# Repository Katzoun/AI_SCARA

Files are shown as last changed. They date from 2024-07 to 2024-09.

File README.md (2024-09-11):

# **AI.SCARA** – The low-cost SCARA robot 
## Abstract
The aim of this project was to design and build a low-cost robot based on the industrial concept SCARA, which meets the requirements in terms of rigidity and repeatability for application in a wide range of manipulation tasks primarily implemented in a university environment. The project includes not only the mechanical design, but also design and implementation of the electrical circuitry, control system, and design of a human-machine graphical interface for basic controland diagnosis of the robotic structure.
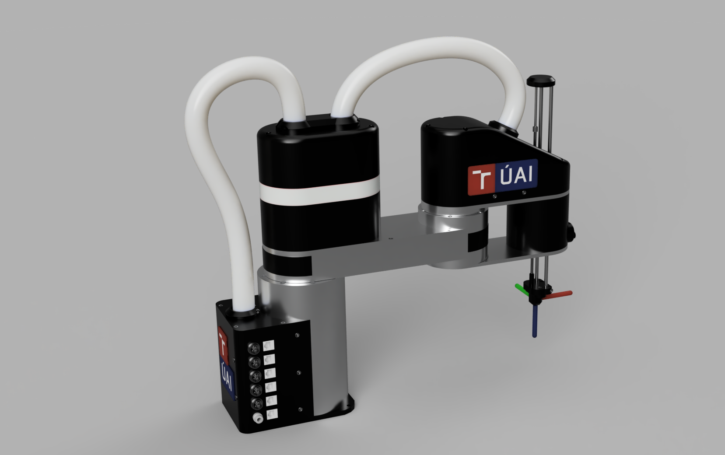
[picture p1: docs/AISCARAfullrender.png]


## Video demontration
Watch the video (https://youtube.com/watch?v=5lQ4tVK84JA)
## Repository Index
* [AISCARA_ControlSystem](https://github.com/Katzoun/AI_SCARA/tree/main/AISCARA_ControlSystem) - Source codes for AISCARA control system
* [AISCARA_GUI](https://github.com/Katzoun/AI_SCARA/tree/main/AISCARA_GUI) - Source codes for AISCARA user interface
* [docs](https://github.com/Katzoun/AI_SCARA/tree/main/docs) - Misc documentation files 
* [parts](https://github.com/Katzoun/AI_SCARA/tree/main/parts) - stl files of all components (with list of all parts)

## Mechanical design
The mechanical structure of the robot consists of aluminium parts combined with 3D printed parts. The combination of 3D printing and metal machining provides good rigidity and a reasonable price. In addition, all metal components are designed to be manufactured on conventional machines (mill and lathe) without numerical control. The mechanical design also includes the design of the electrical control cabinet. All parts of the robot were designed in Fusion 360.

The robot design consists of three key units - **the stationary base, the first arm and the second arm.** 
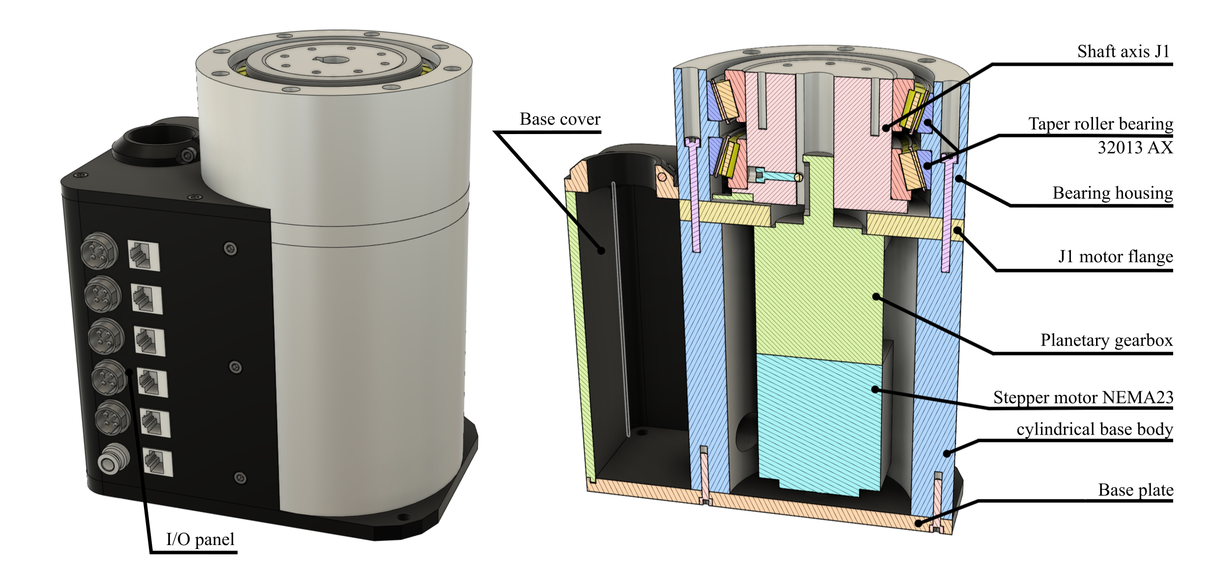
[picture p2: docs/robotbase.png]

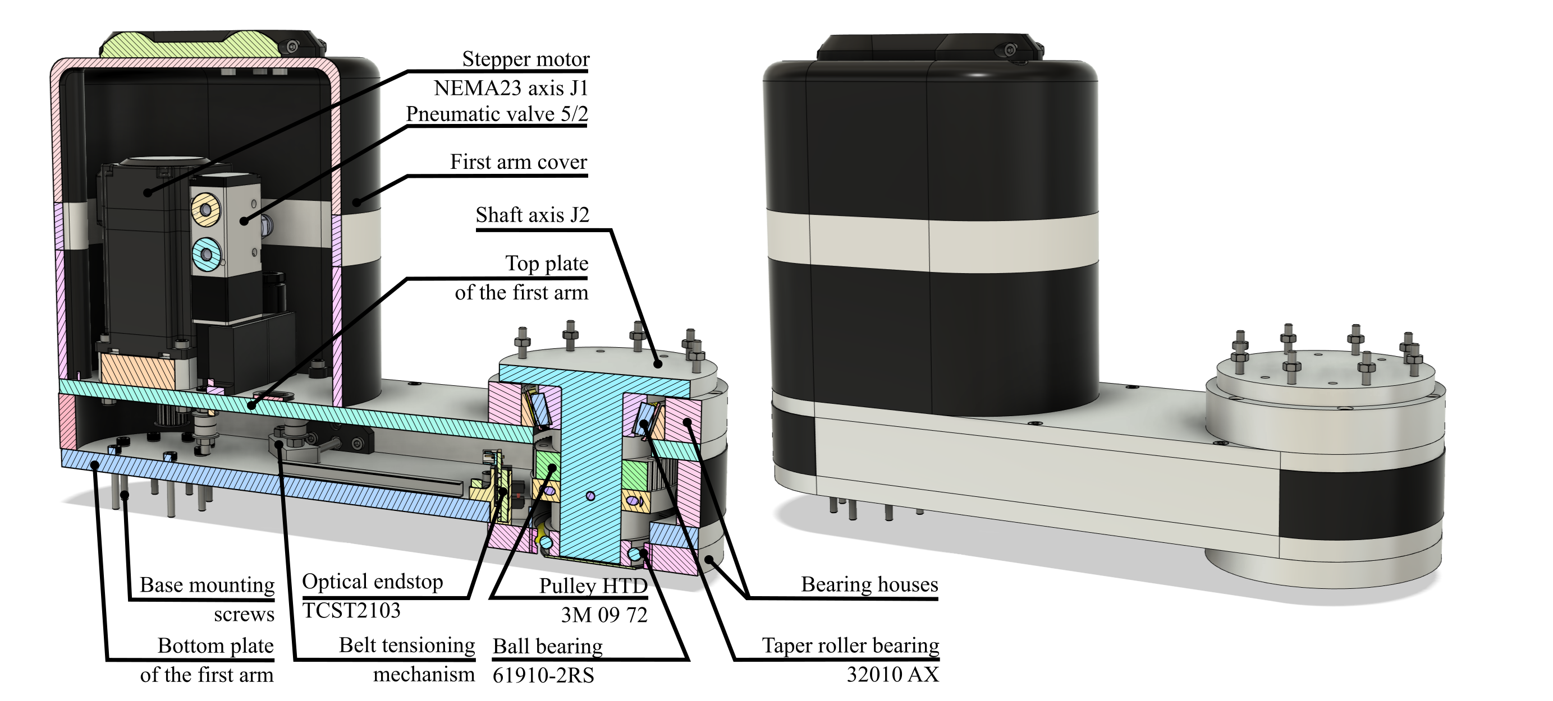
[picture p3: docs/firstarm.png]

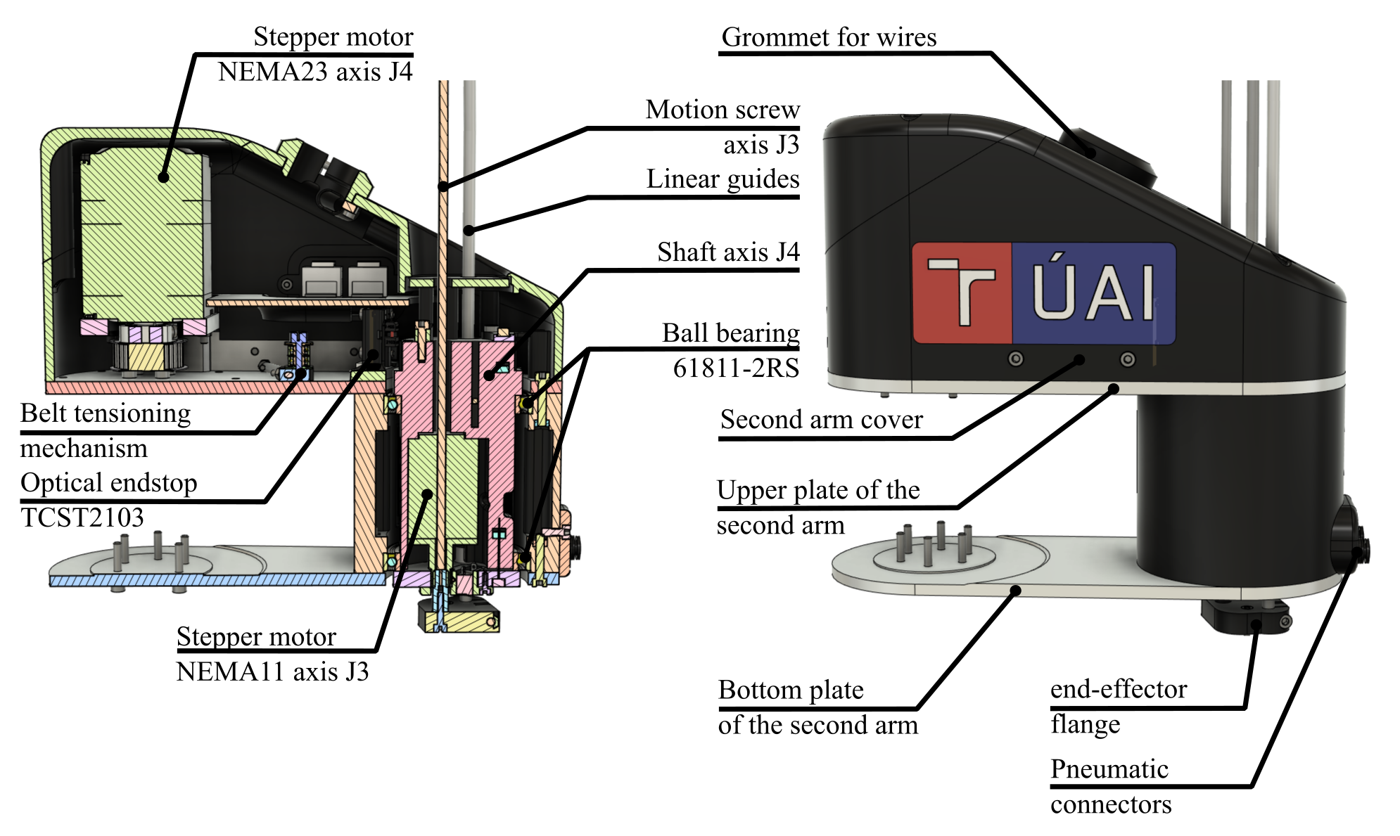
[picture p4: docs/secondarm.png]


## Electrical design
Stepper motors with encoders were chosen to drive the robot. The main advantage of these motors is their very low purchase price compared to equally powerful servo drives. By controlling stepper motors in a closed loop, better dynamic characteristics can be achieved compared to open-loop stepper motors. Another indisputable advantage of closed-loop control is the possibility of position correction in case of overload. Reference position detection is provided by optical limit switches (TCST2103).

**List of used stepper motors** 
* J1 - NEMA23 [23HS22-2804-ME1K ](https://www.omc-stepperonline.com/nema-23-closed-loop-stepper-motor-1-2nm-166-7oz-in-with-magnetic-encoder-1000ppr-4000cpr-23hs22-2804-me1k) with precision planetary gearbox VRL-070C
* J2 - NEMA23 [1-CL57T-S20-V41 ](https://www.omc-stepperonline.com/ts-series-2-0-nm-283-28oz-in-1-axis-closed-loop-stepper-cnc-kit-nema-23-motor-driver-1-cl57t-s20-v41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)
* J3 - NEMA11 [11N18S0754GD-250RS ](https://www.omc-stepperonline.com/nema-11-non-captive-46mm-stack-0-75a-lead-2-54mm-0-1-length-250mm-11n18s0754gd-250rs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)
* J4 - NEMA23 [1-CL57T-S12-V41 ](https://www.omc-stepperonline.com/ts-series-1-2-nm-170oz-in-1-axis-closed-loop-stepper-cnc-kit-nema-23-motor-driver-1-cl57t-s12-v41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)

The robot controller (shown below) brings together all the electronic components necessary for the proper functioning of the AI.SCARA robot - i.e. stepper motor controllers, microcontrollers that run the control system, power supplies and many others. Power is provided by three DC power supplies - LRS-350-36 (CL57 stepper drivers), LRS-100-12 (pneumatic equipment, DM320T driver, internal air compressors etc.) and RS-25-5 (MCUs).

There are two microcontrollers in the SCARA robot controller. The main MCU is the Teensy 4.1, which performs all the kinematic calculations for the robot's movements.
The reason for choosing the Teensy 4.1 microcontroller for robot motion control was mainly due to its architecture, which is compatible with user-friendly Arduino microcontrollers. The control of the robot peripherals is provided by Arduino Nano. 

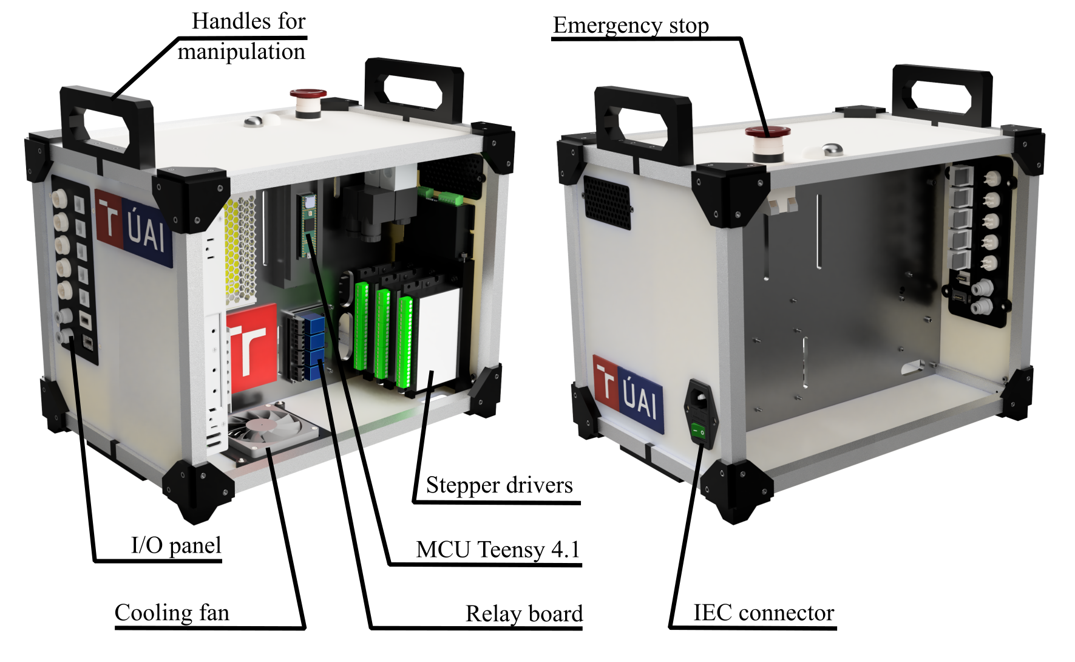
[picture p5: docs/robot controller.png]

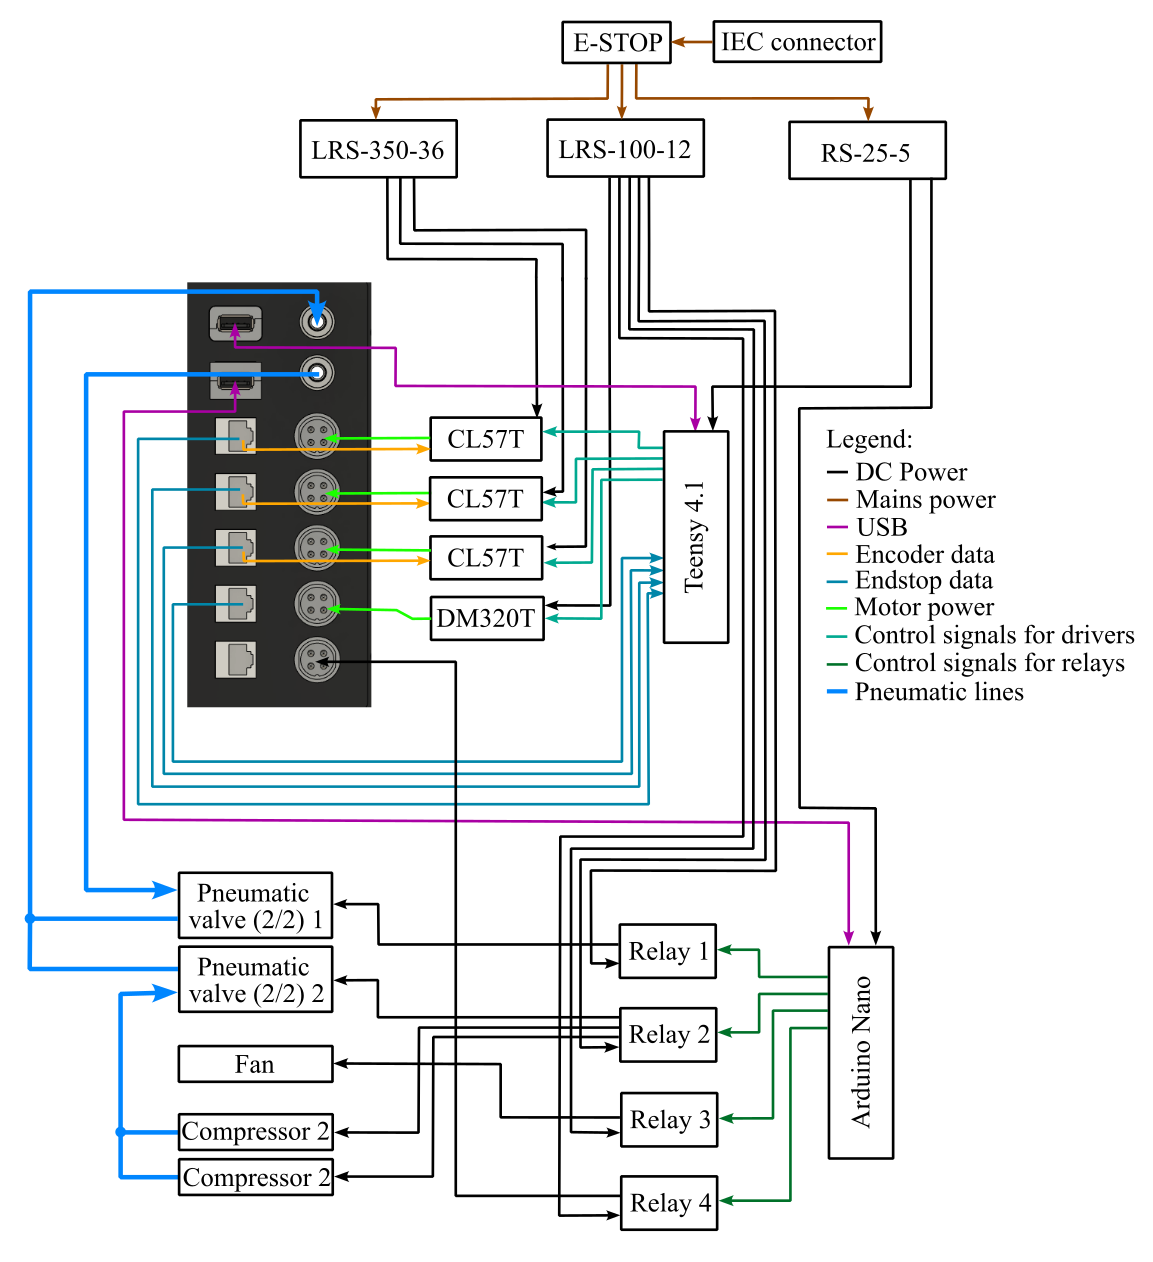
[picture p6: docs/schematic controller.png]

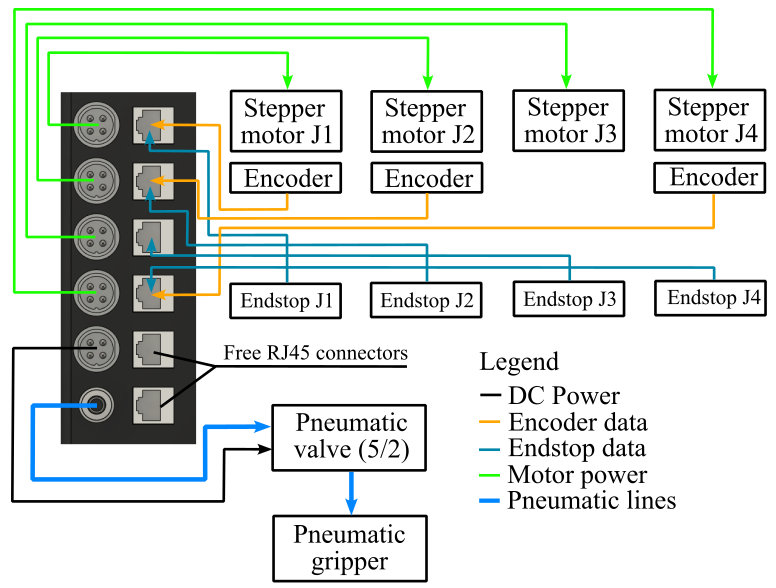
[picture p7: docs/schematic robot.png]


## Software

The control software is a key component of the robotic arm. The proposed system simultaneously performs the control and precise synchronization of all four axes of the robot, analytically solves kinematic calculations for maximum computational efficiency, controls the current position of the axes and, last but not least, controls the robot peripherals. 
**The control software running in the robot controller consists of two parts:**

* [AISCARA teensy board](https://github.com/Katzoun/AI_SCARA/tree/main/AISCARA_ControlSystem/AISCARA%20teensy%20board)
* [AISCARA nano board](https://github.com/Katzoun/AI_SCARA/tree/main/AISCARA_ControlSystem/AISCARA%20nano%20board)

For easy interaction with the robot, a user-friendly graphical interface has been created that allows, among other things, simple diagnostics and programming of the robot's movements.

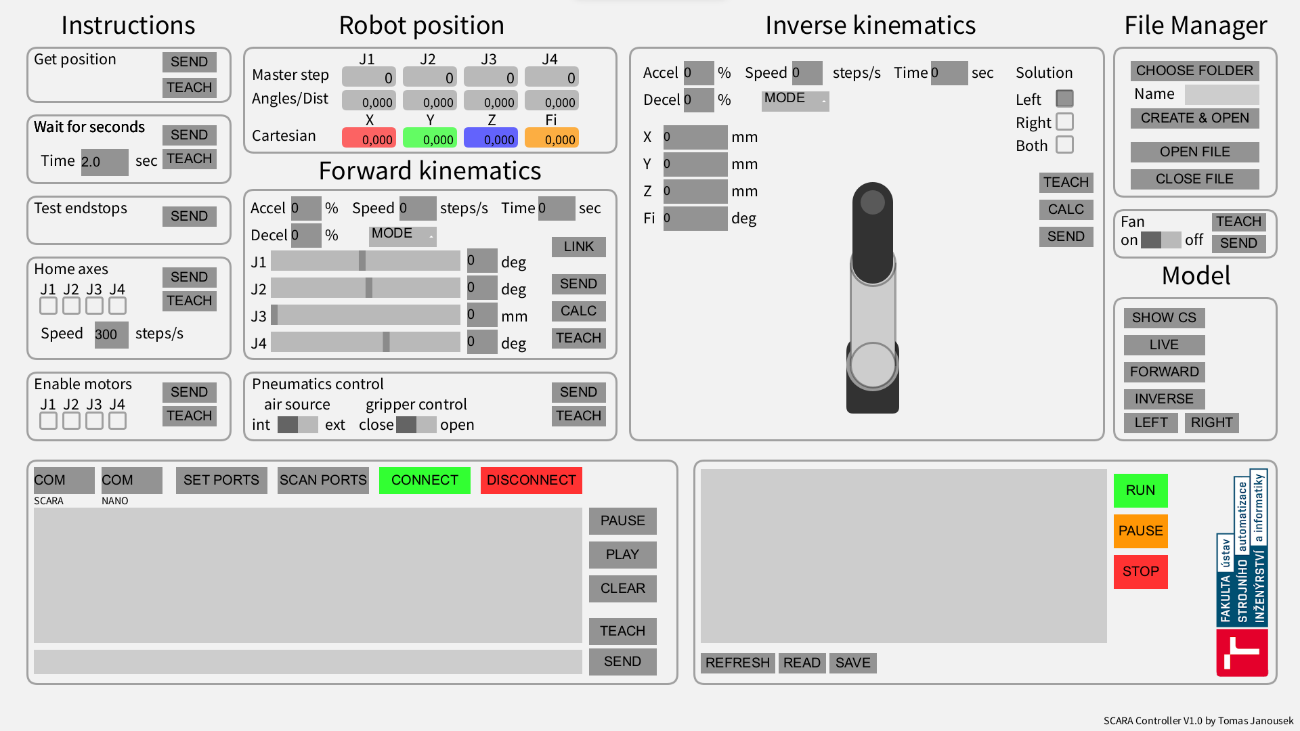
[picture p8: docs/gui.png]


In the lower left corner there is a console where error messages and other information concerning the controller operation are displayed. Below the console there is a command line for manual instruction input. Manual input is particularly useful when testing additional programmed functionalities that are not represented graphically in the interface. To visually check the robot's position, the interface also includes a dynamic 2D model that can operate in three modes. In Live mode, the model displays the position in which the robot is currently physically located. The remaining modes (Forward and Inverse) are simulation modes and are used to visually represent the forward and inverse kinematics solutions. 

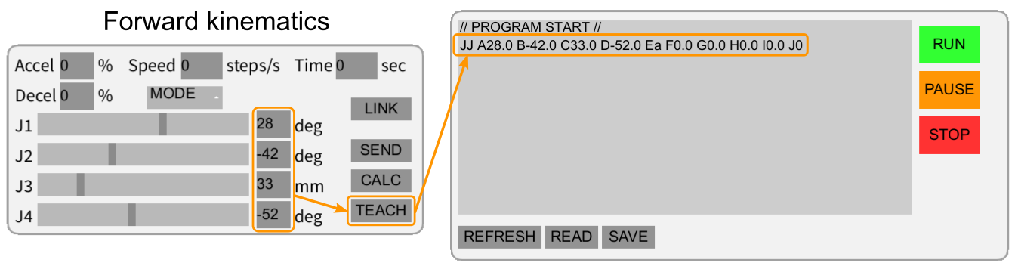
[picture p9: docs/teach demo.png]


Within the proposed interface, the SCARA robot can also be easily programmed in addition to those already mentioned. For most of the instructions, there is a "Teach" button which saves the instruction into the program memory. The entire program is then displayed in a text box to the right of the console. For working with program files, there is a simple file manager in the GUI. Through it you can open already created programs or create completely new ones.

### Establishing communication with the AI.SCARA robot controller
For successful communication between the personal computer and the controller it is first necessary to connect these units via the USB interface. The "scan ports" button is intended to make it easier to find the ports to which the controller is connected. After pressing the "scan ports" button, the console lists the currently used ports of the personal computer. The user interface cannot yet automatically detect which of these ports the controller is on, so the user must manually enter the port names in the appropriate fields. The process of establishing a connection can be initiated with the "connect" button. The connection process is shown in the figure below.
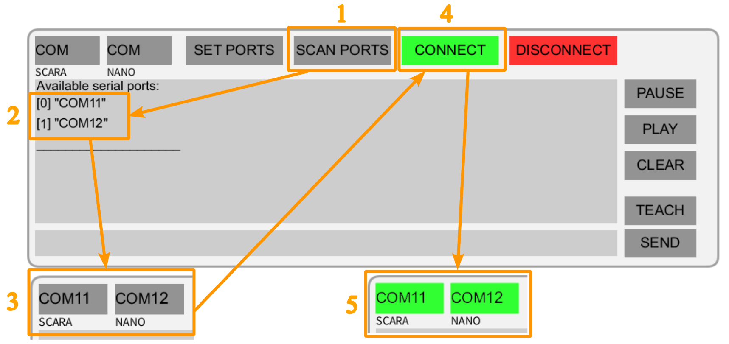
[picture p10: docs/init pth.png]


## Result
After successful assembly and debugging, the designed robotic structure was subjected to a series of tests aimed at verifying the basic "metrological" characteristics of the robot. The measurements performed were divided into three main categories - repeatability tests, stiffness tests and complex tests, which are a combination of the previous two. The repeatability of the robot was estimated to be within a few tenths of a millimetre based on the tests performed. 
Again, it should be noted that the measurements made provide only a very basic idea of the metrological characteristics of the proposed solution. The measurement results are influenced not only by the mechanical design but also by the motion control of the robot. A more precise set of validation tests, including a more advanced statistic evaluation, could be addressed in future work. The table below shows the basic technical parameters of the proposed robot.

| Parameter | Value |
| --- | --- |
| Horizontal reach (X-Y)  | 400 mm  |
| Vertical reach (Z) | 170 mm  |
| Payload | 1 kg |
| Repeatability | tenths of millimetre |
| Max. speed J1 | 120 °/s |
| Max. speed J2 | 120 °/s |
| Max. speed J3 | 80 mm/s |
| Max. speed J4 | 160 °/s |
| Axis range J1 | -116° to +125° |
| Axis range J2 | -129° to +120° |
| Axis range J3 | 170 mm |
| Axis range J4 | -190° to +120° |
| Robot weight | 17 kg |
| Controller weight | 8 kg |
| Build price | approx. 1500 €| 

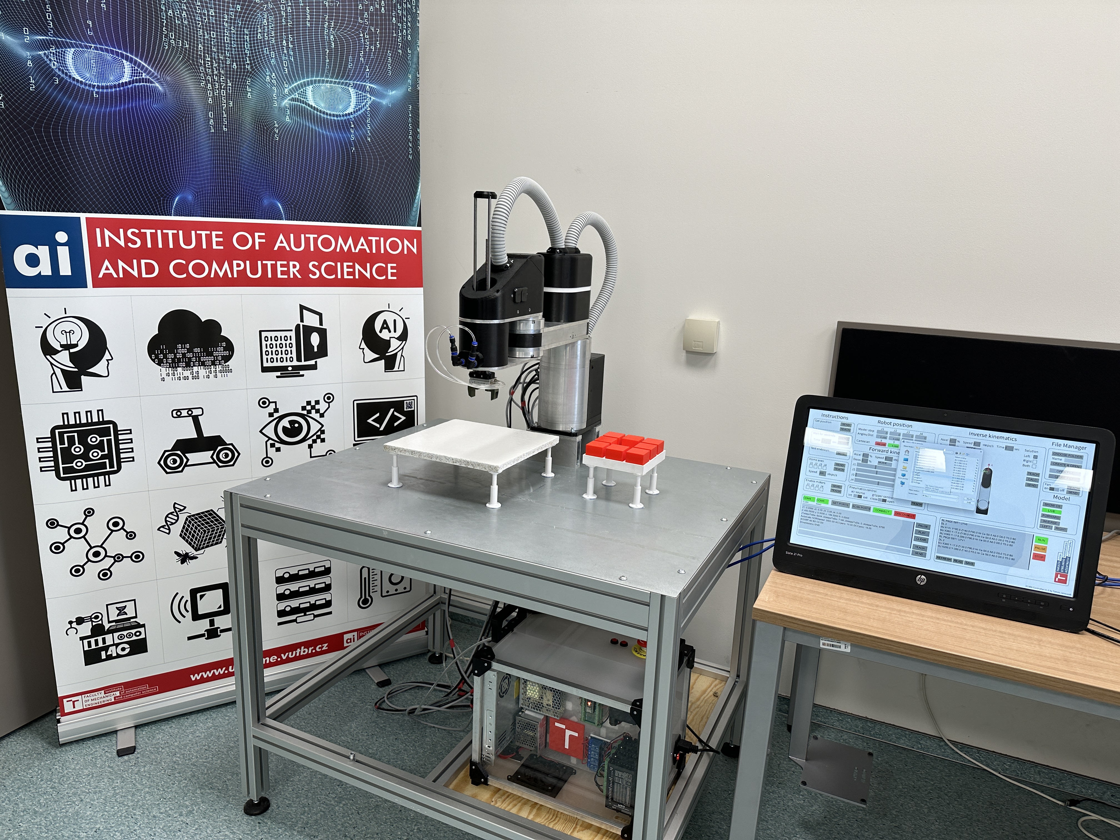
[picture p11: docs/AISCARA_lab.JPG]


## Contact info
For more information and details about this project please contact me on
tomas.janousek02@gmail.com

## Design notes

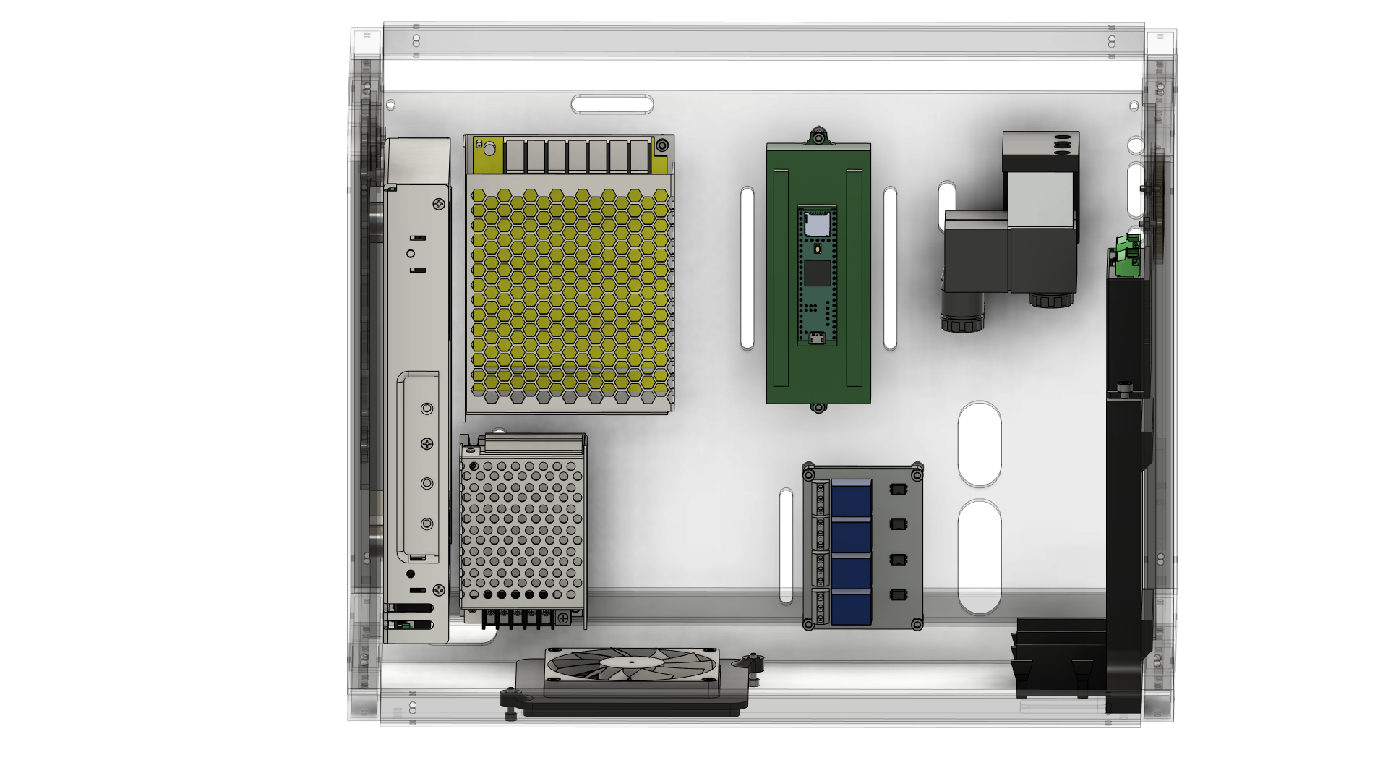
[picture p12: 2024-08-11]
docs/img controller/controlbox op20 v1.png

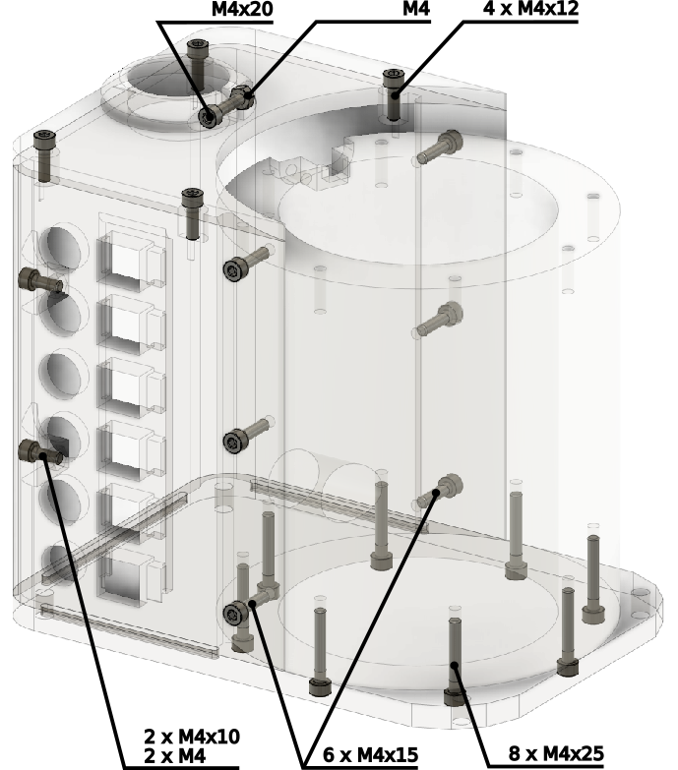
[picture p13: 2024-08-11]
docs/img base/base1 pth.png

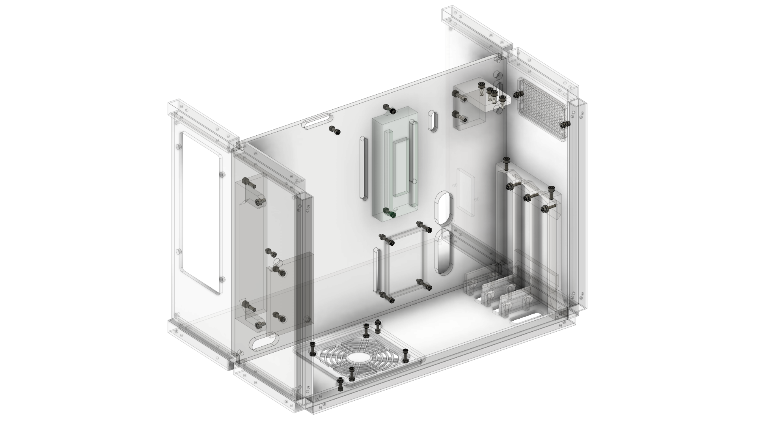
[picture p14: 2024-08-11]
docs/img controller/controlbox op20 v6.png

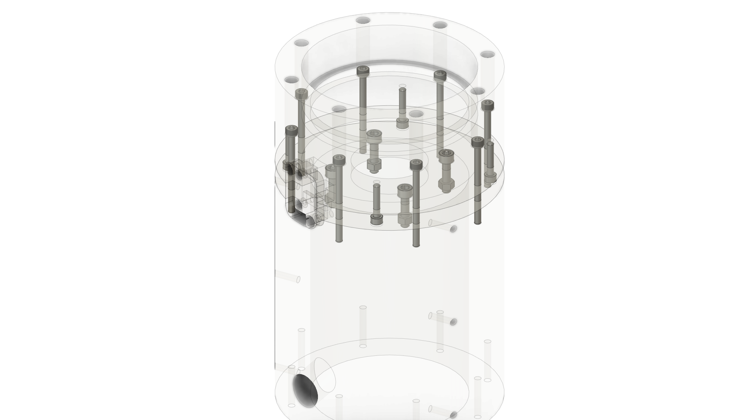
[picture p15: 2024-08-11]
docs/img base/base2.png

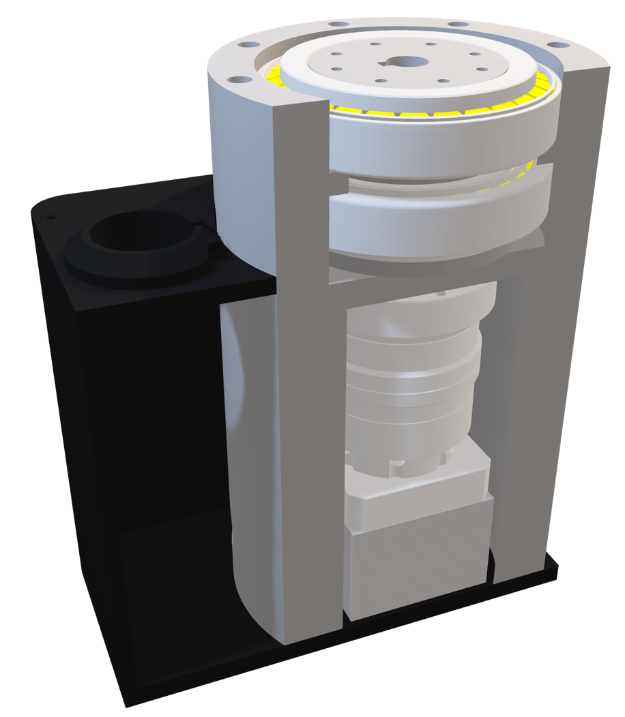
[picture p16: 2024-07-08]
docs/base.png

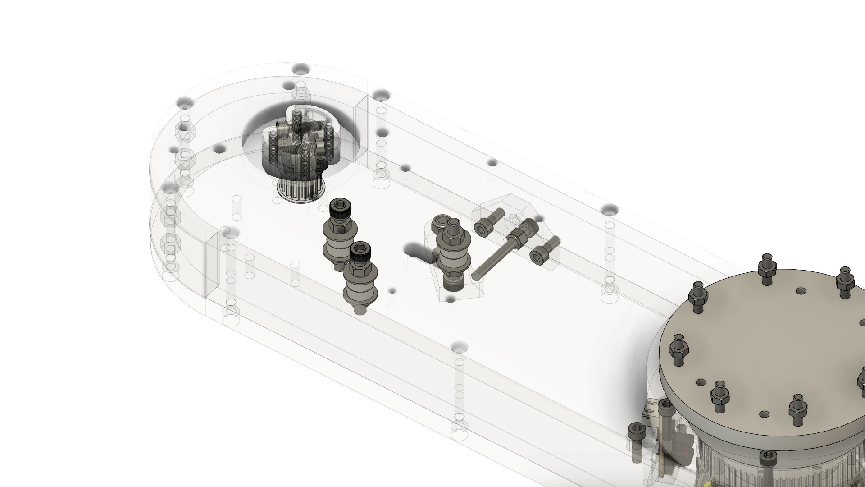
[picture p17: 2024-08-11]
docs/img first arm/arm 3 prev v63 3.png

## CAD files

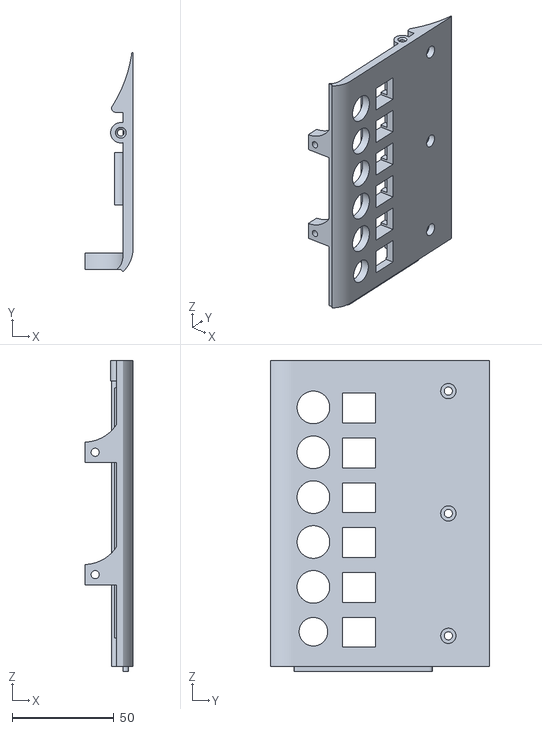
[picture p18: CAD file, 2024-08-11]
parts/base/Base cover (front).stl
23.5 x 107.6 x 152.5

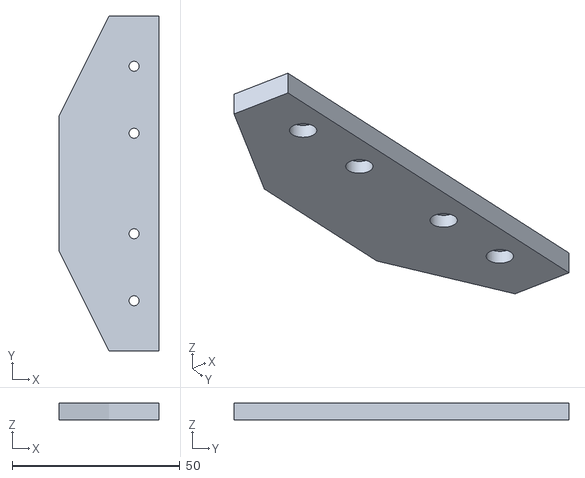
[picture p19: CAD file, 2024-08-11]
parts/controller/Longitudinal control box cover.stl
30.0 x 100.0 x 5.00

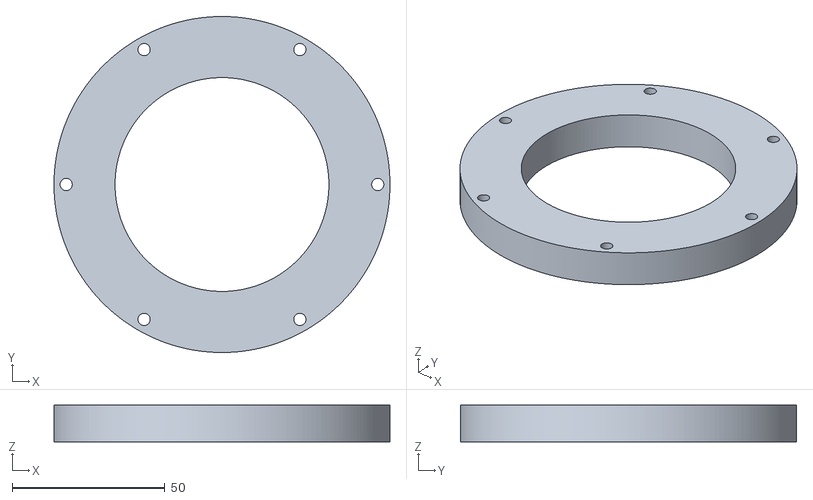
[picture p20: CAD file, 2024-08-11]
parts/first arm/First arm bearing housing (bottom).stl
110.0 x 110.0 x 12.0

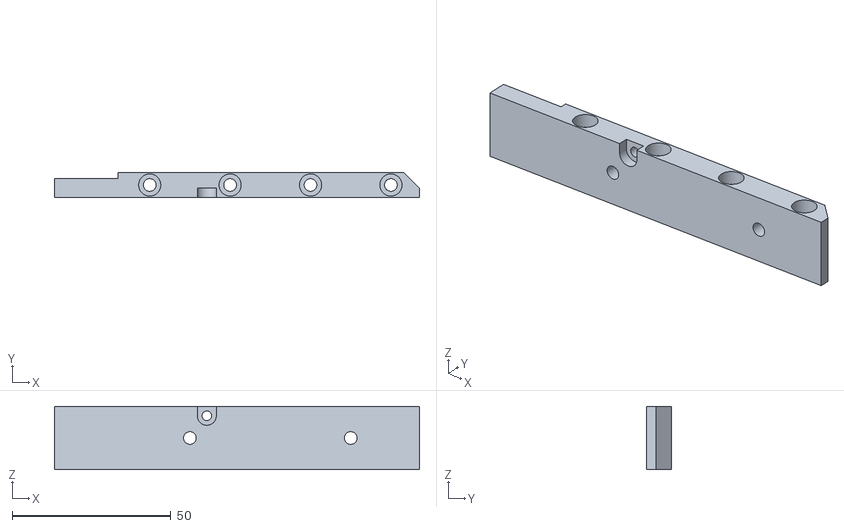
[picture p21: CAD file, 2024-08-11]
parts/second arm/Second arm reinforcement.stl
115.0 x 8.00 x 20.0

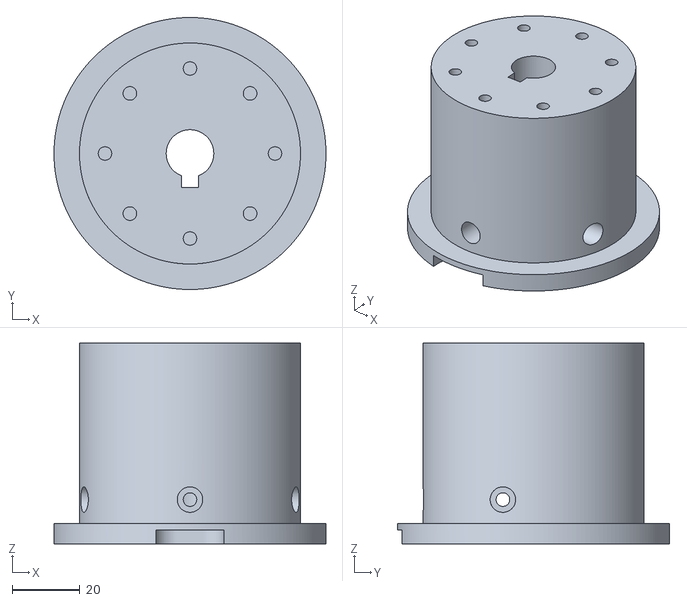
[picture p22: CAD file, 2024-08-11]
parts/base/Shaft axis J1.stl
80.0 x 80.0 x 59.0

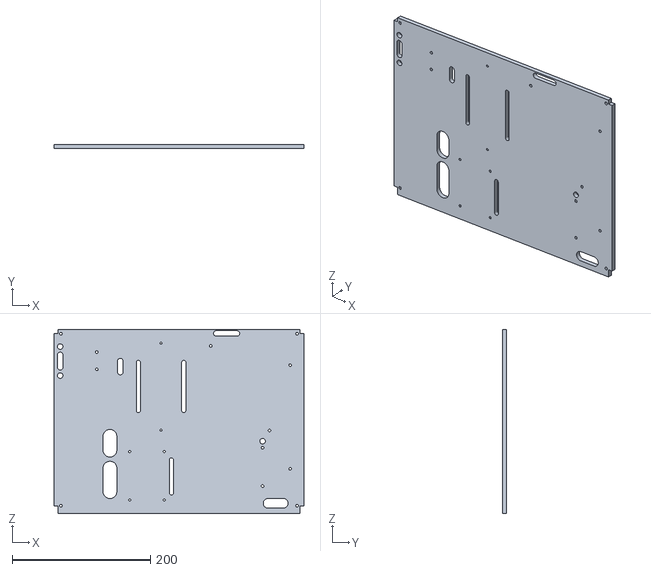
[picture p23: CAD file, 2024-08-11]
parts/controller/White plexiglass 362x267x6 mm - middle panel.stl
362.0 x 6.00 x 267.0

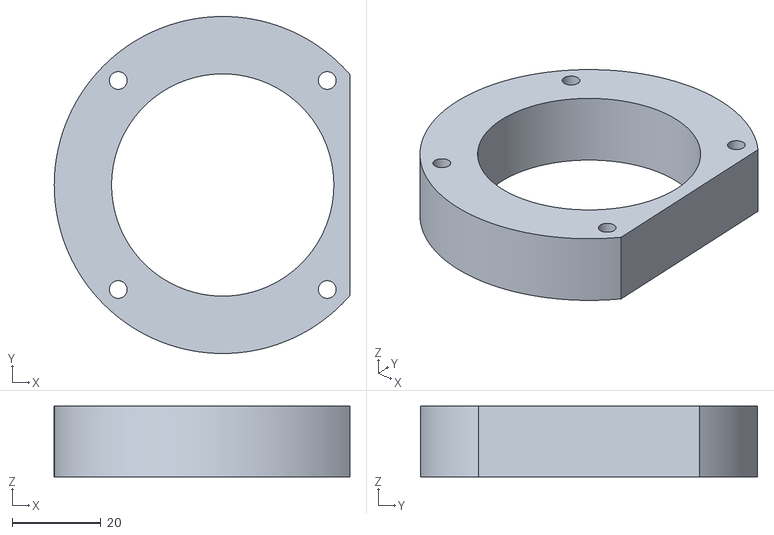
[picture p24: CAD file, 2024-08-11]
parts/first arm/J2 motor mount.stl
66.6 x 76.0 x 16.0

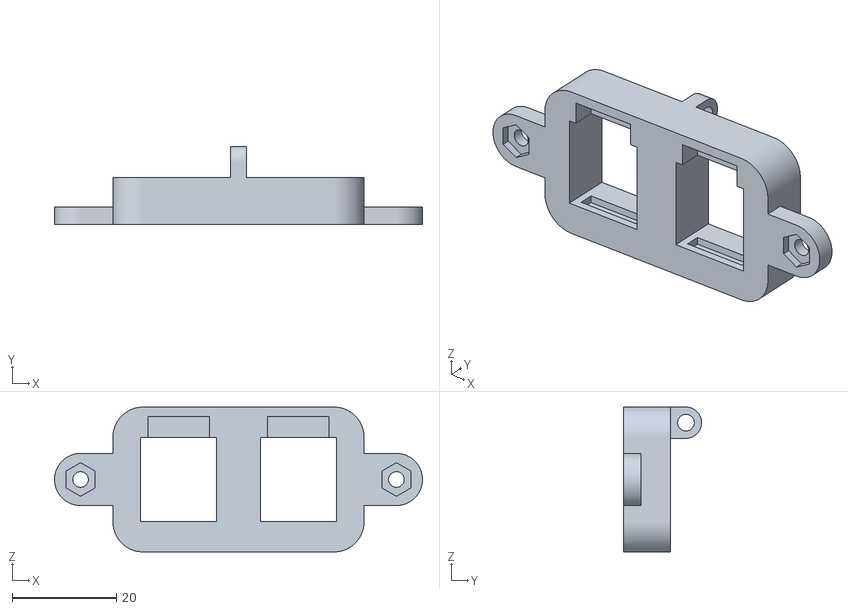
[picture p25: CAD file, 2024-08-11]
parts/second arm/RJ45 connector holder.stl
70.6 x 15.0 x 27.8

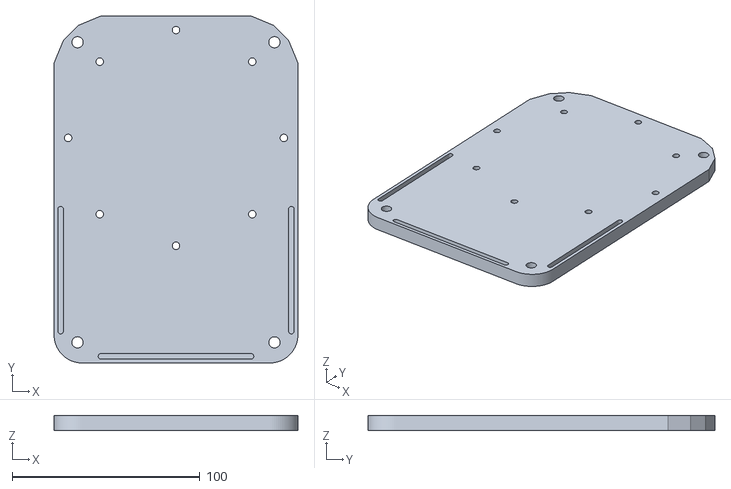
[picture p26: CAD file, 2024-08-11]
parts/base/Base plate.stl
130.0 x 185.0 x 8.00

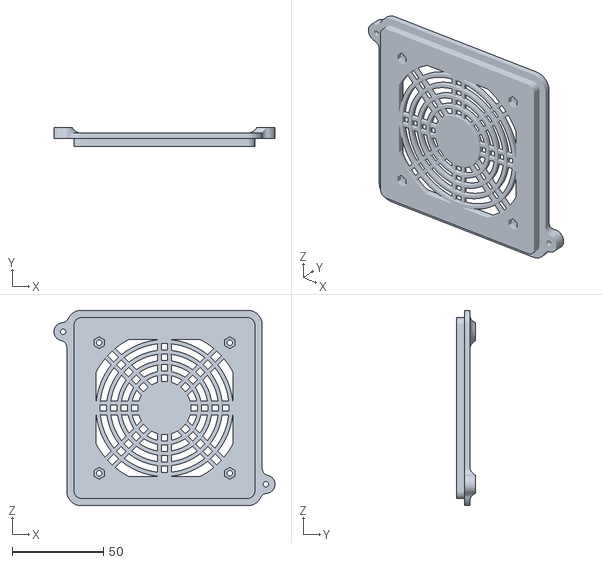
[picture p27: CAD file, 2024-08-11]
parts/controller/Fan holder.stl
121.0 x 10.2 x 107.0

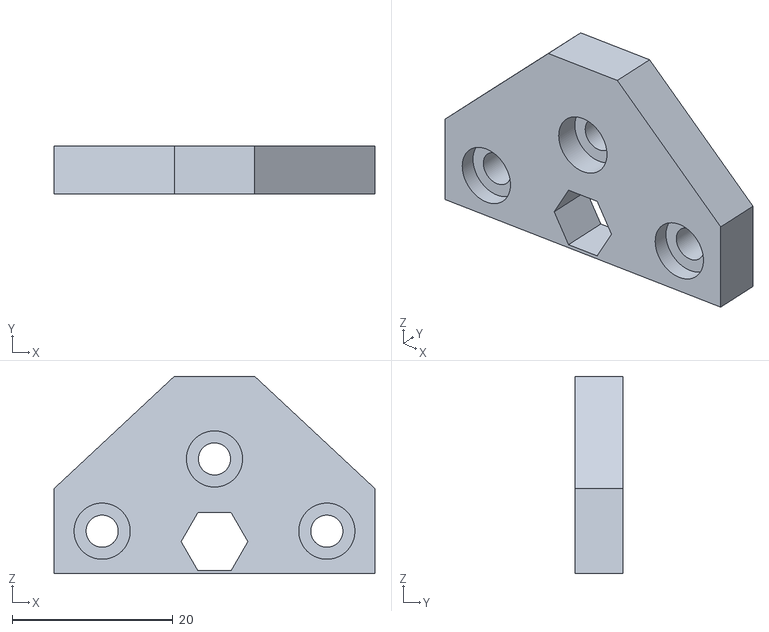
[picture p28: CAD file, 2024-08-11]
parts/first arm/Tension pulley holder J2.stl
40.0 x 6.00 x 24.6

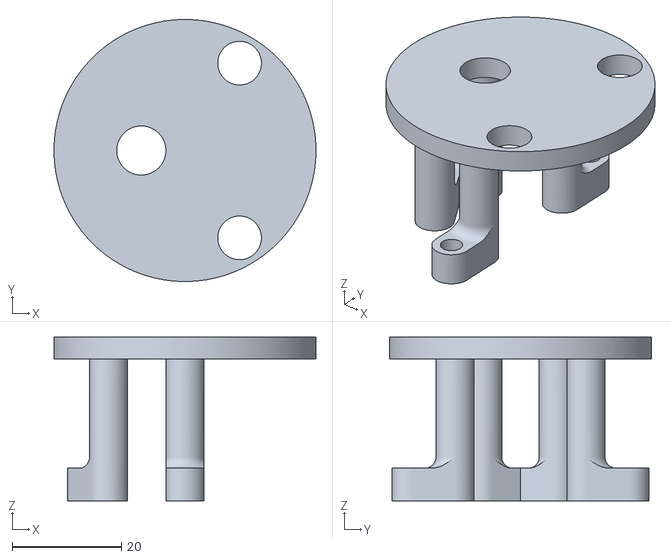
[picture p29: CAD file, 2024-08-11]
parts/second arm/J4 shaft cover.stl
48.0 x 48.0 x 30.0

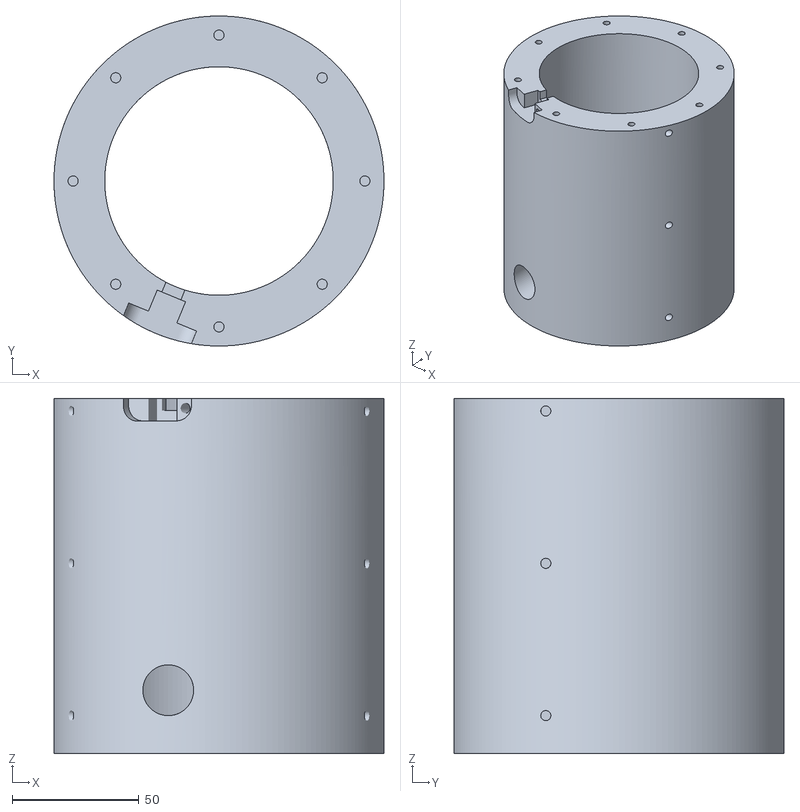
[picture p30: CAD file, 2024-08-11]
parts/base/Cylindrical base body.stl
130.0 x 130.0 x 140.0

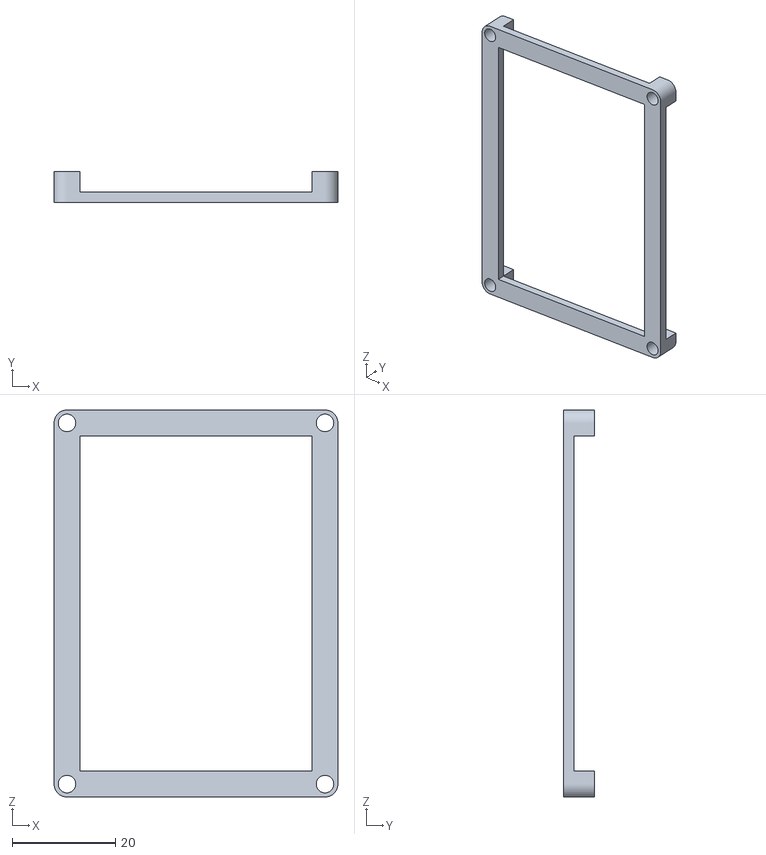
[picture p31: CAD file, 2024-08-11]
parts/controller/Relay board holder.stl
55.0 x 6.00 x 75.0

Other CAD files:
parts/first arm/Wall of the first arm (cylindrical part).stl
parts/second arm/Bottom plate of the second arm.stl
parts/base/Base cover (top).stl
parts/controller/Corner control box cover.stl
parts/base/Base bearing housing.stl
parts/base/Endstop J1.stl
parts/base/J1 motor flange.stl
parts/base/Limit switch holder J1.stl
parts/controller/Control box handles.stl
parts/controller/Corner control box coupling.stl
parts/controller/Corner control box cover with legs.stl
parts/controller/IO panel.stl
parts/controller/Longitudinal control box coupling.stl
parts/controller/Pneumatic valve holder.stl
parts/controller/Power supply holder (LRS-350-36).stl
parts/controller/Power supply holder (S-25-5).stl
parts/controller/Square rod 15x15x1,5 mm – 110 mm.stl
parts/controller/Square rod 15x15x1,5 mm – 250 mm.stl
parts/controller/Square rod15x15x1,5 mm – 350 mm.stl
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

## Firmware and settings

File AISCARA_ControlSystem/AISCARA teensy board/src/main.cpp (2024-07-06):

#include <Arduino.h>
#include <math.h>

// Converts degrees to radians. M_PI is defined in <math.h>.
#define degreesToRadians(angleDegrees) (angleDegrees * M_PI / 180.0)

// Converts radians to degrees.
#define radiansToDegrees(angleRadians) (angleRadians * 180.0 / M_PI)

// speed profile variables
struct Point
{
  long x;
  long y;
};
class Curve // class for storing bezier curve control points
{
public:
  Point start;
  Point control1; // control points for bezier curve
  Point control2;
  Point end;
};

// define pins for motors
#define J1stepPin 16
#define J1dirPin 20

#define J2stepPin 17
#define J2dirPin 21

#define J3stepPin 19
#define J3dirPin 23

#define J4stepPin 18
#define J4dirPin 22

#define J1enablePin 41
#define J2enablePin 40
#define J3enablePin 15
#define J4enablePin 14

#define J1calPin 24
#define J2calPin 25
#define J3calPin 26
#define J4calPin 27

// calibration rotation direction
#define J1caldir 0
#define J2caldir 0
#define J3caldir 1
#define J4caldir 0

// default rotation direction change if needed
#define J1rotdir 1
#define J2rotdir 1
#define J3rotdir 0
#define J4rotdir 1

// steps per revolution for each motor
#define J1stepsPerRev 20000.0 // microstepping 800 , ratio 25:1
#define J2stepsPerRev 20000.0 // microstepping 5000, ratio 4:1
#define J3stepsPerRev 200.0   // microstepping on driver is set to 400 but for better performance of the robot it is set in software to 200 
#define J4stepsPerRev 16666.666666666666666666666666667// microstepping 10000, ratio 1,6666666666666666666666666666667:1

#define J1stepsPerDeg 55.55555555555556
#define J2stepsPerDeg 55.55555555555556
#define J3stepsPerMM  78.74015748031496 //(previously was 157,4803149606299) 2.54mm per rev
#define J4stepsPerDeg 46.29629629629630

// robot axis limits
#define J1LimPos 125.0
#define J1LimNeg -116.0
#define J2LimPos 120.0
#define J2LimNeg -129.0
#define J3LimUpper 0.0
#define J3LimLower 170.0
#define J4LimPos 120.0
#define J4LimNeg -190.0

// steps from home position to zero position
int J1StepsDef = int(J1LimNeg * J1stepsPerDeg);
int J2StepsDef = int(J2LimNeg * J2stepsPerDeg);
int J3StepsDef = int(J3LimUpper * J3stepsPerMM);
int J4StepsDef = int(J4LimNeg * J4stepsPerDeg);

int J1MaxStepsPos = int(J1LimPos * J1stepsPerDeg);
int J2MaxStepsPos = int(J2LimPos * J2stepsPerDeg);
int J3MaxStepsPos = int(J3LimLower * J3stepsPerMM);
int J4MaxStepsPos = int(J4LimPos * J4stepsPerDeg);

String cmdbuff3;
String cmdbuff2;
String cmdbuff1;
String receivedData;
String processedData;
String instruction;

int debug = 0;
unsigned long previousMillis = 0;
const long interval = 300; // interval at which to blink (milliseconds)

// global robot position vars - absolute steps from home position
int32_t J1stepsMaster = 0;
int32_t J2stepsMaster = 0;
int32_t J3stepsMaster = 0;
int32_t J4stepsMaster = 0;

// ================== ROBOT PARAMETERS ==================
// robot kinematic parameters
float L1 = 250.0;
float L2 = 150.0;
float d1 = 217.0;
float dcor = 22.5;
int kinError = 0;
int gripperSymetry = 0;

// forward kinematics solution variables
float fw_x = 0;
float fw_y = 0;
float fw_z = 0;
float fw_fi = 0;

// inverse kiknematics variables  //J3 and J4 need to be changed
float inv_J1deg[2] = {0.0, 0.0}; // left and right solution
float inv_J2deg[2] = {0.0, 0.0};
float inv_J3distance = 0.0;
float inv_J4deg[2] = {0.0, 0.0};

int leftHandedPossible = 0;
int rightHandedPossible = 0;

// enum TeensyStates
enum TeensyStates
{
  IDLE,
  PROCESSING_INSTRUCTION,
  CLEARING_BUFFER1,
  // instructions
  DL, // delay - wait for time in ms - this function is blocking
  EN, // enable motors
  HS, // home to limit switches until all switches are triggered
  JJ, // jog joints
  MJ, // move joints
  KF, // forward kinematics test
  TL, // test limit switches
  TD, // test drive motors
  RP, // robot position

} TeensyState;

// ================== KINEMATIC FUNCTIONS ==================
void ForwardKinematicsSolver(float J1angle, float J2angle, float J3distance, float J4angle)
{
  float J1angleRad = degreesToRadians(J1angle);
  float J2angleRad = degreesToRadians(J2angle);
  float J4angleRad = degreesToRadians(J4angle);
  fw_x = L1 * cos(J1angleRad) + L2 * cos(J1angleRad + J2angleRad);
  fw_y = L1 * sin(J1angleRad) + L2 * sin(J1angleRad + J2angleRad);
  fw_z = d1 - J3distance - dcor;
  fw_fi = radiansToDegrees((J1angleRad + J2angleRad + J4angleRad));
}
void InverseKinematicsSolver(float inv_x, float inv_y, float inv_z, float inv_fi)
{
  kinError = 0; // reset the error flag
  float J4angleSolLeftRadAlt2 = 0;
  float J4angleSolLeftRadAlt3 = 0;
  float J4angleSolRightRadAlt2 = 0;
  float J4angleSolRightRadAlt3 = 0;

  // calculate the angle of the second joint
  float inv_fiRad = degreesToRadians(inv_fi);
  float acosArg = (pow(inv_x, 2) + pow(inv_y, 2) - pow(L1, 2) - pow(L2, 2)) / (2 * L1 * L2);
  if (acosArg > 1.0 || acosArg < -1.0)
  {
    kinError = 1;
    return;
  }
  float J2angleSolRightRad = acos(acosArg);
  float J2angleSolLeftRad = -J2angleSolRightRad;
  // calculate the angle of the first joint
  float J1angleSolRightRad = atan2(L2 * sin(J2angleSolLeftRad) * inv_x + (L1 + L2 * cos(J2angleSolLeftRad)) * inv_y, (L1 + L2 * cos(J2angleSolLeftRad)) * inv_x - L2 * sin(J2angleSolLeftRad) * inv_y);
  float J1angleSolLeftRad = -J1angleSolRightRad + 2 * atan2(inv_y, inv_x);
  // calculate the angle of the third joint
  float J4angleSolLeftRad = inv_fiRad - J1angleSolLeftRad - J2angleSolLeftRad;
  float J4angleSolRightRad = inv_fiRad - J1angleSolRightRad - J2angleSolRightRad;

  inv_J3distance = d1 - inv_z - dcor;

  // corrections for different quadrants
  // J1 angle left solution correction
  if (J1angleSolLeftRad > M_PI)
  {
    J1angleSolLeftRad = J1angleSolLeftRad - M_TWOPI;
  }

  if (J1angleSolLeftRad < -M_PI)
  {
    J1angleSolLeftRad = M_TWOPI + J1angleSolLeftRad;
  }
  // J1 angle right solution correction
  if (J1angleSolRightRad > M_PI)
  {
    J1angleSolRightRad = J1angleSolRightRad - M_TWOPI;
  }

  if (J1angleSolRightRad < -M_PI)
  {
    J1angleSolRightRad = J1angleSolRightRad + M_TWOPI;
  }
  // J3 angle left solution correction
  if (J4angleSolLeftRad < -M_PI)
  {
    J4angleSolLeftRad = J4angleSolLeftRad + M_TWOPI;
  }
  if (J4angleSolLeftRad > M_PI)
  {
    J4angleSolLeftRad = J4angleSolLeftRad - M_TWOPI;
  }
  // J3 angle right solution correction
  if (J4angleSolRightRad < -M_PI)
  {
    J4angleSolRightRad = J4angleSolRightRad + M_TWOPI;
  }
  if (J4angleSolRightRad > M_PI)
  {
    J4angleSolRightRad = J4angleSolRightRad - M_TWOPI;
  }
  if (J4angleSolRightRad < -M_TWOPI)
  {
    J4angleSolRightRad = J4angleSolRightRad + M_TWOPI;
  }

  // convert the angles to degrees
  inv_J1deg[0] = radiansToDegrees(J1angleSolLeftRad);
  inv_J1deg[1] = radiansToDegrees(J1angleSolRightRad);
  inv_J2deg[0] = radiansToDegrees(J2angleSolLeftRad);
  inv_J2deg[1] = radiansToDegrees(J2angleSolRightRad);
  inv_J3distance = d1 - inv_z - dcor; // entire calculation for z axis
  inv_J4deg[0] = radiansToDegrees(J4angleSolLeftRad);
  inv_J4deg[1] = radiansToDegrees(J4angleSolRightRad);
}
void checkLimitsInverse()
{
  leftHandedPossible = 0;
  rightHandedPossible = 0;
  // check if the solution is possible
  if (((J1LimNeg < inv_J1deg[0]) && (inv_J1deg[0] < J1LimPos)) && ((J2LimNeg < inv_J2deg[0]) && (inv_J2deg[0] < J2LimPos)) && ((J4LimNeg < inv_J4deg[0]) && (J4LimPos > inv_J4deg[0])))
  {
    leftHandedPossible = 1;
  }
  else
  {
    Serial.println("left handed solution is over angle limits");
  }

  if (((J1LimNeg < inv_J1deg[1]) && (inv_J1deg[1] < J1LimPos)) && ((J2LimNeg < inv_J2deg[1]) && (inv_J2deg[1] < J2LimPos)) && ((J4LimNeg < inv_J4deg[1]) && (J4LimPos > inv_J4deg[1])))
  {
    rightHandedPossible = 1;
  }
  else
  {
    Serial.println("right handed solution is over angle limits");
  }
}
int checkLimitsForward(float J1angle, float J2angle, float J3distance, float J4angle) // has to be checked
{
  int forwardKinematicError = 1;
  // check if the solution is possible
  if ((J1LimNeg <= J1angle) && (J1angle <= J1LimPos) && (J2LimNeg <= J2angle) && (J2angle <= J2LimPos) && (J4LimNeg <= J4angle) && (J4LimPos >= J4angle) && (J3LimLower >= J3distance) && (J3distance >= J3LimUpper)) // LimLower = positive // LimUpper = negative
  {
    forwardKinematicError = 0;
  }
  else
  {
    forwardKinematicError = 0;
  }
  return forwardKinematicError;
}

// ================ FUNCTIONS ====================
void shiftbuffarray()
{
  if (cmdbuff1 == "")
  {
    // shift 2 to 1
    cmdbuff1 = cmdbuff2;
    cmdbuff2 = "";
  }
  if (cmdbuff2 == "")
  {
    // shift 3 to 2
    cmdbuff2 = cmdbuff3;
    cmdbuff3 = "";
  }
  if (cmdbuff1 == "")
  {
    // shift 2 to 1
    cmdbuff1 = cmdbuff2;
    cmdbuff2 = "";
  }
}
void processSerial()
{
  if (Serial.available() > 0 and cmdbuff3 == "")
  {
    char received = Serial.read();
    receivedData = receivedData + received;
    // Serial.println(receivedData);

    if (received == '\n')
    {
      // Serial.println("end of line detected");
      cmdbuff3 = receivedData;
      receivedData = "";
      shiftbuffarray();
    }
  }
}
void blinkLed()
{
  unsigned long currentMillis = millis();

  // led blink to show that the program is running
  if (currentMillis - previousMillis >= interval) // blink led
  {
    previousMillis = currentMillis;
    digitalWrite(13, !digitalRead(13)); // led is sign of life
  }
}
float getPointOnBZCurve(float percentComplete, Point start, Point control1, Point control2, Point end)
{
  float BP1 = percentComplete * percentComplete * percentComplete;                   // t^3
  float BP2 = 3 * percentComplete * percentComplete * (1 - percentComplete);         // 3t^2(1-t)
  float BP3 = 3 * percentComplete * (1 - percentComplete) * (1 - percentComplete);   // 3t(1-t)^2
  float BP4 = (1 - percentComplete) * (1 - percentComplete) * (1 - percentComplete); // (1-t)^3

  // float x = start.x * BP1 + control1.x * BP2 + control2.x * BP3 + end.x * BP4;

  float y = start.y * BP1 + control1.y * BP2 + control2.y * BP3 + end.y * BP4;
  return y;
}
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
void loop()
{
  blinkLed();
  processSerial();

  switch (TeensyState)
  {
  // ========================== IDLE ==========================
  case IDLE:
  {
    if (cmdbuff1 != "")
    {
      TeensyState = PROCESSING_INSTRUCTION;
      break;
    }
  }
  break;
  // ================== PROCESSING INSTRUCTION ==================
  case PROCESSING_INSTRUCTION:
  {
    processedData = cmdbuff1;                    // copy the string from the buffer1 to currently processed string
    processedData.trim();                        // remove whitespaces from the string
    instruction = processedData.substring(0, 2); // get the first 2 characters of the string (the instruction)
    processedData = processedData.substring(3);

    if (instruction == "DL")
    {
      if (debug == 1 || debug == 2)
        Serial.println("delay instruction detected");
      TeensyState = DL;
      break;
    }
    if (instruction == "HS")
    {
      if (debug == 1 || debug == 2)
        Serial.println("home to limit switches instruction detected");
      TeensyState = HS;
      break;
    }
    if (instruction == "EN")
    {
      if (debug == 1 || debug == 2)
        Serial.println("enable motors instruction detected");
      TeensyState = EN;
      break;
    }
    if (instruction == "KF")
    {
      if (debug == 1 || debug == 2)
        Serial.println("forward kinematics instruction detected");
      TeensyState = KF;
      break;
    }
    if (instruction == "JJ")
    {
      if (debug == 1 || debug == 2)
        Serial.println("jog joints instruction detected");
      TeensyState = JJ;
      break;
    }
    if (instruction == "MJ")
    {
      if (debug == 1 || debug == 2)
        Serial.println("MOVEJ instruction detected");
      TeensyState = MJ;
      break;
    }
    if (instruction == "TL")
    {
      if (debug == 1 || debug == 2)
        Serial.println("test limit switches instruction detected");
      TeensyState = TL;
      break;
    }
    if (instruction == "TD")
    {
      if (debug == 1 || debug == 2)
        Serial.println("test drive function instruction detected");
      TeensyState = TD;
      break;
    }
    if (instruction == "RP")
    {
      if (debug == 1 || debug == 2)
        Serial.println("send robot position instruction detected");
      TeensyState = RP;
      break;
    }
    else
    {
      Serial.println("no valid instruction detected, going idle");
      TeensyState = CLEARING_BUFFER1;
      break;
    }
  }
  break;

  // ================== DELAY FOR TIME ==================
  case DL:
  {
    int TimeStartIndex = processedData.indexOf("T");
    float waitingTime = processedData.substring(TimeStartIndex + 1).toFloat();   // get the value after the T character and convert it to float
    waitingTime = waitingTime * 1000;                                            // convert the value to milliseconds
    delay(waitingTime);                                                          // delay for that amount of time
    Serial.println("ACKDL delay for " + String(waitingTime / 1000) + " seconds done"); // print the delay time
    TeensyState = CLEARING_BUFFER1;
  }
  break;

  // ================== TEST LIMIT SWITCHES ==================
  case TL:
  {
    for (int i = 0; i < 5000; i++)
    {

      if (digitalRead(J1calPin) == HIGH)
      {
        Serial.println(F("J1 limit switch triggered"));
      }
      if (digitalRead(J2calPin) == HIGH)
      {
        Serial.println(F("J2 limit switch triggered"));
      }
      if (digitalRead(J3calPin) == HIGH)
      {
        Serial.println(F("J3 limit switch triggered"));
      }
      if (digitalRead(J4calPin) == HIGH)
      {
        Serial.println(F("J4 limit switch triggered"));
      }
      delay(5);
    }
    TeensyState = CLEARING_BUFFER1;
  }
  break;

  // ================== ENABLE MOTORS ==================
  case EN:
  {
    Serial.println(processedData);
    int indexJ1 = processedData.indexOf('A');
    int indexJ2 = processedData.indexOf('B');
    int indexJ3 = processedData.indexOf('C');
    int indexJ4 = processedData.indexOf('D');

    int J1enable = processedData.substring(indexJ1 + 1, indexJ1 + 2).toInt();
    int J2enable = processedData.substring(indexJ2 + 1, indexJ2 + 2).toInt();
    int J3enable = processedData.substring(indexJ3 + 1, indexJ3 + 2).toInt();
    int J4enable = processedData.substring(indexJ4 + 1, indexJ4 + 2).toInt();
    String sendBack = "ACKEN A" + String(J1enable) + "B" + String(J2enable) + "C" + String(J3enable) + "D" + String(J4enable);
    Serial.println(sendBack);
    if (J1enable == 1)
    {
      digitalWrite(J1enablePin, HIGH);
    }
    else
    {
      digitalWrite(J1enablePin, LOW);
    }
    if (J2enable == 1)
    {
      digitalWrite(J2enablePin, HIGH);
    }
    else
    {
      digitalWrite(J2enablePin, LOW);
    }
    if (J3enable == 1)
    {
      digitalWrite(J3enablePin, HIGH);
    }
    else
    {
      digitalWrite(J3enablePin, LOW);
    }
    if (J4enable == 1)
    {
      digitalWrite(J4enablePin, HIGH);
    }
    else
    {
      digitalWrite(J4enablePin, LOW);
    }
    TeensyState = CLEARING_BUFFER1;
  }
  break;

  // ================== HOME TO LIMIT SWITCHES INIT==================
  case HS:
  {
    Serial.println(processedData);

    int indexJ1 = processedData.indexOf('A');
    int indexJ2 = processedData.indexOf('B');
    int indexJ3 = processedData.indexOf('C');
    int indexJ4 = processedData.indexOf('D');
    int SPstart = processedData.indexOf('S');

    int J1home = processedData.substring(indexJ1 + 1, indexJ1 + 2).toInt();
    int J2home = processedData.substring(indexJ2 + 1, indexJ2 + 2).toInt();
    int J3home = processedData.substring(indexJ3 + 1, indexJ3 + 2).toInt();
    int J4home = processedData.substring(indexJ4 + 1, indexJ4 + 2).toInt();
    int SpeedIn = processedData.substring(SPstart + 1).toInt();

    //  RESET COUNTERS
    int J1stepsDone = 0;
    int J2stepsDone = 0;
    int J3stepsDone = 0;
    int J4stepsDone = 0;

    int J1pass = 0;
    int J2pass = 0;
    int J3pass = 0;
    int J4pass = 0;
    int J3homed = 0;
    int iter1 = 0;
    int speed = 0;

    if (J1home == 0 && J2home == 0 && J3home == 0 && J4home == 0)
    {
      Serial.println(F("No axis selected for homing, going idle"));
      TeensyState = CLEARING_BUFFER1;
      break;
    }
    if (SpeedIn == 0)
    {
      Serial.println(F("no speed set, going idle"));
      TeensyState = CLEARING_BUFFER1;
      break;
    }
    if (SpeedIn > 500)
    {
      Serial.println(F("speed too high (>500), going idle"));
      TeensyState = CLEARING_BUFFER1;
      break;
    }

    if (J2home || J1home || J4home)
    {
      J3home = 1; // if J1 J2 or J4 is selected for homing, J3 will be homed as well (to avoid collision with the connector panel)
    }
    int stepTimeCalc = (1000000 / SpeedIn);
    if (debug == 1 || debug == 2)
      Serial.println(stepTimeCalc);

    // SET DIRECTIONS
    //  J1 //
    if (J1caldir == 1)
    {
      digitalWrite(J1dirPin, LOW);
    }
    else if (J1caldir == 0)
    {
      digitalWrite(J1dirPin, HIGH);
    }

    // J2 //
    if (J2caldir == 1)
    {
      digitalWrite(J2dirPin, LOW);
    }
    else if (J2caldir == 0)
    {
      digitalWrite(J2dirPin, HIGH);
    }
    // J3 //
    if (J3caldir == 1)
    {
      digitalWrite(J3dirPin, LOW);
    }
    else if (J3caldir == 0)
    {
      digitalWrite(J3dirPin, HIGH);
    }

    // J4 //
    if (J4caldir == 1)
    {
      digitalWrite(J4dirPin, LOW);
    }
    else if (J4caldir == 0)
    {
      digitalWrite(J4dirPin, HIGH);
    }

    delayMicroseconds(50);
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

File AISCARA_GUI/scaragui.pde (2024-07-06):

import processing.serial.*;
import controlP5.*;
import static processing.core.PApplet.*;


ControlP5 cp5;
Serial scaraSerial;
Serial nanoSerial;

PImage logoUAI;

String SCARAport = "";
String NANOport = "";
Textarea cons, programArea;
Println console;
int  scaraConnected = 0;
int nanoConnected = 0;
String receivedDataScara = "";
String receivedDataNano = "";
String processedDataScara = "";
String processedDataNano = "";
String folderPath = "";
String filePath = "";
boolean showCoordinateSys = false;
DropdownList ddlCotrolMode, ddlCotrolModeInverse ;
PrintWriter openedFile;
CheckBox enableCheckbox, homeCheckbox;
boolean toggleAirGripper= false;
boolean toggleAirSource = false;
boolean toggleFan = false;
int J1stepsMaster=0;
int J2stepsMaster=0;
int J3stepsMaster=0;
int J4stepsMaster=0;
int modelMode = 0;
int previousModelMode = 0;
boolean programRunning = false;
boolean ACKreceived = false;
boolean firstLine = false;
int lineNumber = 0;
String[] programLines;
RadioButton solutionButtons;
boolean inverseModel = false;
boolean forwardLinked = false;

float previousJ1Val=0;
float previousJ2Val=0;
float previousJ3Val=0;
float previousJ4Val=0;

final float J1stepsPerDeg = 55.55555555555556;
final float J2stepsPerDeg = 55.55555555555556;
final float J3stepsPerMM  = 78.74015748031496;
final float J4stepsPerDeg = 46.29629629629630;

float J1LimPos =125.0;
float J1LimNeg =-116.0;
float J2LimPos =120.0;
float J2LimNeg =-129.0;
float J3LimUpper= 0.0;
float J3LimLower =170.0;
float J4LimPos =120.0;
float J4LimNeg =-190.0;

// ================== ROBOT PARAMETERS ==================
// robot kinematic parameters
float L1 = 250.0;
float L2 = 150.0;
float d1 = 217.0;
float dcor = 22.5;
int kinError = 0;
int gripperSymetry = 0;

// forward kinematics solution variables
float fw_x = 0;
float fw_y = 0;
float fw_z = 0;
float fw_fi = 0;

float fw_xMaster=0;
float fw_yMaster=0;
float fw_zMaster=0;
float fw_fiMaster=0;

float[] inv_J1deg = {0.0, 0.0}; // left and right solution
float[] inv_J2deg = {0.0, 0.0};
float inv_J3distance = 0.0;
float[] inv_J4deg = {0.0, 0.0};

int leftHandedPossible = 0;
int rightHandedPossible = 0;

int i = 570;
int j = -200;


void setup() {
  fullScreen(2);
  //size(1920, 1080);
  logoUAI = loadImage("UAIlogoVert.png");
  cp5 = new ControlP5(this);
  PFont pfont = createFont("Arial", 25, true);
  ControlFont font = new ControlFont(pfont, 20);
  ControlFont font2 = new ControlFont(pfont, 18);
  cons = cp5.addTextarea("txt")
    .setPosition(50, 750)
    .setSize(810, 200)
    .setFont(createFont("Arial", 18))
    .setLineHeight(24)
    .setColor(color(0))
    .setColorBackground(color(0, 100))
    .setColorForeground(color(255, 100));
  ;
  console = cp5.addConsole(cons);

  cp5.addTextfield("SCARAport")
    .setPosition(50, 690)
    .setSize(90, 40)
    .setFont(font)
    .setAutoClear(false)
    .setColor(color(0))
    .setCaptionLabel("")
    .setColorBackground(color(0, 100))
    .setColorForeground(color(255, 1))
    .setColorActive(color(0, 0))
    .setText("COM")
    ;

  cp5.addTextfield("NANOport")
    .setPosition(150, 690)
    .setSize(90, 40)
    .setCaptionLabel("")
    .setFont(font)
    .setAutoClear(false)
    .setColor(color(0))
    .setColorBackground(color(0, 100))
    .setColorForeground(color(255, 1))
    .setColorActive(color(0, 0))
    .setText("COM")
    ;
  cp5.addButton("setPorts")
    .setPosition(260, 690)
    .setSize(135, 40)
    .setFont(font)
    .setCaptionLabel("set ports")
    .setColorBackground(color(0, 100))
    .setColorActive(color(20, 85))
    .setColorForeground(color(20, 70))
    .setColorCaptionLabel(255)
    ;
  cp5.addButton("refreshPorts")
    .setPosition(410, 690)
    .setSize(135, 40)
    .setFont(font)
    .setCaptionLabel("scan ports")
    .setColorBackground(color(0, 100))
    .setColorActive(color(0, 85))
    .setColorForeground(color(50, 70))
    .setColorCaptionLabel(255)
    ;
  cp5.addButton("connectPorts")
    .setPosition(560, 690)
    .setSize(135, 40)
    .setFont(font)
    .setCaptionLabel("Connect")
    .setColorBackground(color(50, 255, 50, 255))
    .setColorActive(color(10, 255, 10, 255))
    .setColorForeground(color(100, 255, 100, 255))
    .setColorCaptionLabel(255)
    ;
  cp5.addButton("disconnectPorts")
    .setPosition(710, 690)
    .setSize(150, 40)
    .setFont(font)
    .setCaptionLabel("Disconnect")
    .setColorBackground(color(255, 50, 50, 255))
    .setColorActive(color(255, 10, 10, 255))
    .setColorForeground(color(255, 100, 100, 255))
    .setColorCaptionLabel(255)
    ;


  //console control buttons

  cp5.addButton("pauseCons")
    .setPosition(870, 750)
    .setSize(100, 40)
    .setFont(font)
    .setCaptionLabel("pause")
    .setColorBackground(color(0, 100))
    .setColorActive(color(20, 85))
    .setColorForeground(color(20, 70))
    .setColorCaptionLabel(255)
    ;
  cp5.addButton("playCons")
    .setPosition(870, 800)
    .setSize(100, 40)
    .setFont(font)
    .setCaptionLabel("play")
    .setColorBackground(color(0, 100))
    .setColorActive(color(20, 85))
    .setColorForeground(color(20, 70))
    .setColorCaptionLabel(255)
    ;
  cp5.addButton("clearCons")
    .setPosition(870, 850)
    .setSize(100, 40)
    .setFont(font)
    .setCaptionLabel("clear")
    .setColorBackground(color(0, 100))
    .setColorActive(color(20, 85))
    .setColorForeground(color(20, 70))
    .setColorCaptionLabel(255)
    ;

  //enable motors
  enableCheckbox = cp5.addCheckBox("enableCheckbox")
    .setPosition(60, 610)
    .setColorBackground(color(20, 1))
    .setColorActive(color(0, 100))
    .setColorForeground(color(10, 150))
    .setSize(24, 24)
    .setItemsPerRow(4)
    .setSpacingColumn(10)
    .addItem("J1ena", 1)
    .addItem("J2ena", 1)
    .addItem("J3ena", 1)
    .addItem("J4ena", 1)
    .hideLabels();
  ;
  cp5.addButton("enaSend")
    .setPosition(240, 565)
    .setSize(80, 30)
    .setFont(font)
    .setCaptionLabel("SEND")
    .setColorBackground(color(0, 100))
    .setColorActive(color(20, 85))
    .setColorForeground(color(20, 70))
    .setColorCaptionLabel(255)
    ;
  cp5.addButton("enaTeach")
    .setPosition(240, 565+35)
    .setSize(80, 30)
    .setFont(font)
    .setCaptionLabel("Teach")
    .setColorBackground(color(0, 100))
    .setColorActive(color(20, 85))
    .setColorForeground(color(20, 70))
    .setColorCaptionLabel(255)
    ;
  //home axes checkbox
  homeCheckbox = cp5.addCheckBox("homeCheckbox")
    .setPosition(60, 440)
    .setColorBackground(color(20, 1))
    .setColorActive(color(0, 100))
    .setColorForeground(color(10, 150))
    .setSize(24, 24)
    .setItemsPerRow(4)
    .setSpacingColumn(10)
    .addItem("J1home", 1)
    .addItem("J2home", 1)
    .addItem("J3home", 1)
    .addItem("J4home", 1)
    .hideLabels();
  ;
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

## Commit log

2024-07-06 schematics added
2024-08-11 added partlist and stl files
    [Base bearing housing.stl, Base cover (front).stl, Base cover (top).stl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]
